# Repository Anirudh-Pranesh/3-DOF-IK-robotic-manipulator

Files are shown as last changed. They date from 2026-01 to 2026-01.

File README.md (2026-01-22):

# 3-DOF-Inverse-kinematic-robotic-manipulator

This project is an attempt at making a 3 degree of freedom robotic manipulator and implementing basic inverse kinematics

### Project contributors : 

- **Electronics and Programming :**
    -  Anirudh Pranesh - Eletronics and communication engineering department, National Institute of Technology Karnataka,  batch of 29'
- **Mathematical analsyses and assistance :** 
    - Neo Anil Dodti - Electronics and communication engineering department, National Institute of Technology Karnataka, batch of 29'
    - Aman Tandon - Electronics and communication engineering department, National Institute of Technology Karnataka, batch of 29'
- **Mechanical design :**
    - Maxon David Nazareth - Mechanical engineering department, National Institute of Technology Karnataka, batch of 29'

## The robotic manipulator and degrees of freedom 

The arm like structure of an industrial robot which is used to manipulate materials without direct physical ccontact by the operator is known as a robotic manipulator. A 3 degree of freedom robotic manipulator 
is designed to mimic the movement of a human arm. The motions achieved by the shoulder, elbows and wrists in a human arm is replicated in robotics using **joints**, **links**, **actuators**, and **end-effectors**

The image below depicts what an industrial grade robotic manipulator looks like



The degrees of freedom (DOF) of a manipulator is one of its defining features and is an important measure of the manipulators mobility and flexibility.

The degree of freedom is the number of independent moements the robot can make. 

## Introduction to the components of a manipulator and the initial design

The components that together constitute a robotic manipulator are **joints**, **links**, **actuators**, and **end-effectors**

1. Joint: A connection between two links that allows relative motion
    - Prismatic joint : Translation / sliding along one axis. Actuating the joint makes it longer/shorter
    - Revolute joint : A rotational joint (analogous to an elbow) that rotates about one degree of freedom
    - Spherial joint : A spherical joint can move in multiple degrees of freedom around a single point (analgous to the shoulder)
2. Link: A rigid body that connects joints and transmits motion and force
3. Actuator: A device that provides motion or force to drive a joint
4. End-effector: The terminal device attached to the last link that performs the task (for example a gripper / a scientific tool)

**The initial design :**

For a 3 DOF robotic manipulator, we fixated on 3 revolute joints. One to act as the shoulder and rotate about the y-axis. The 2nd to again act as a shoulder and rotate about the x-axis and the 3rd to act as the elbow, hence giving us access to any point in 3D space

We chose two, SG90 9g servos and one Futaba S3003 sero motor as the actuators. Ideally an actuator with a cycloidal gearbox should have been used. It offers very little backlash, and converts the high speeds of motors into higher torque to prevent the arm on collapsing on itself (An issue which was encountered later in the development process). However we went with the servo motors due to budget and time constraints.

For the links, we designed two I-beams in Fusion 360 that have a slot to attach the gear of the servo motor, and a hole on the other end to attach the end-effector / the servo motor for the elbow. 

In the end, after multiple centre of mass analsyes in Fusion 360, we determined the arm was stable and went with 3D printing it. We chose our material to be PETG with a 25% infill. 

9AA72045-951F-4C17-9807-37681B96CB96

759E43AC-6026-4F62-A465-EB66088A091E

https://github.com/user-attachments/assets/e654b260-f733-496b-b24b-751bba9cb4f4

## Forward vs Inverse kinematics

In forward kinematics, the operator manually sets the angles at which each joint should be rotated to, in order for its end-effector to reach a particular orientation/location in space.

However in inverse kinematics, the robot is aware of the final orientation/location its end-effector should be at, and it accordingly calculates at what angle each joint should be rotated to. 

For a 3-DOF manipulator, the math is relatively simple, involving inverse trigonometric functions and the cosine rule. However upon increasing the degrees of freedom the math becomes much more complex, involving linear algebra and transformations. 

## Real world applications 

A robotic manipulator is a quintessential technological system in the medical field. They are used in surgical robots and prosthetics. 

These are also often seen in industrial manufacturing processes and also used in space exploration missions. 

All these applications use inverse kinematics and hence it is clearly evident why understanding IK is cornerstone for working towards a career in robotics.

## Electronics and Programming - Inverse kinemtaics implementation 

The entire system is controlled using an arduino uno microcontroller. A unity simulation was set up to form the logical layer. Hence the rotation of each joint calculated via inverse kinematics in unity is obtained and sent to arduino using serial communication, and hence the angles are set to the servo motors using the Servo.h library. 

Here is the specific part of the code that performs the inverse kinematics calculations : 

```C#
// Obtaining traget position 
xf = Target.position.x;
yf = Target.position.y;
zf = Target.position.z;

r = Mathf.Sqrt(Mathf.Pow(xf, 2) + Mathf.Pow(zf, 2)); // Magnitude of the projection of the position vector of final point on the XZ plane
l = Mathf.Sqrt(Mathf.Pow(r, 2) + Mathf.Pow(yf, 2)); // Magnitude of the position vector of the final point

//l1 and l2 are the link lenghts

phi =  Mathf.Acos(((l*l)+(l1*l1)-(l2*l2))/(2*l1*l)) * Mathf.Rad2Deg; // Angle of the first link with respect the the position vector of the final point using cosine rule
theta = Mathf.Atan2(yf, r) * Mathf.Rad2Deg; // angle of the position vector of the final point with the XZ plane

Quaternion a = Quaternion.Euler(0, (180 + Mathf.Atan2(xf, zf) * Mathf.Rad2Deg), 0); // Setting angle for the base (shoulder) joint
Quaternion b = Quaternion.Euler(phi + theta, 0, 0); // Setting angle for the first link 
Quaternion c = Quaternion.Euler(-2 * phi, 0, 0); // Setting angle for the 2nd link (2 * phi assuming the two lengths are equal which it is in our case by design)

// Spherical linear interpolation for a smooth look
transform.localRotation = Quaternion.Slerp(transform.localRotation, a, t * Time.deltaTime);
base_joint.localRotation = Quaternion.Slerp(base_joint.localRotation, b, t * Time.deltaTime);
elbow_joint.localRotation = Quaternion.Slerp(elbow_joint.localRotation, c, t * Time.deltaTime);
```

Here is the fully working simulation : 

https://github.com/user-attachments/assets/3f60e0b6-7de5-4177-973a-fe10abcc836b

## Assembly

Once the 3D printed parts arrived, several **MAJOR** flaws in the mechanical design were immediately obvious.

First and foremost the parts were much heavier than anticipated. In hindsight it would have been a smarter move to make the links thinner and lesser in length
Secondly, the holes made for the gear of the servo motor to slot in were missing gear teeth, hence it was impossible to make the link rotate with the servo motor
Thirdly, the holes made for the servo motor to slot in at the joints had too less clearance

All in all the design was not optimal for the actuators we chose. 

A29553D9-5106-4DBB-A082-6044CEA94357

With some clever engineering, the plastic servo horns that came with the motors were attached to the links using strong rubber bands, and thankfully the link was able to rotate with the motor.

This however led to another issue. Due to the weight of the print being much higher than expected, our initial torque calculations went wrong. The SG90 servo could not provide enough torque at the shoulder to support the first link along with the 2nd link and the elbow joint. Hence, we used the S3003 servo motor with a much higher torque capacity to be the actuator at the shoulder. 

This proved to work and we had achieved 2 degrees of freedom for the robotic manipulator.

However we could not achieve the 3rd degree of freedom. The entire arm was attached to a circular disk which was mounted on to a singular servo motor for the rotation of the manipulator about the y axis. 

The motor could not sustain the weight of the entire system and the disk toppled. Many measures were taken in order to mitigate the ordeal. For example adding counter weights using metal. 
These efforts proved to be futile and we could not achieve the 3rd DOF. The gripper could not be attached either due to further excessive weight.  

We decided to work with the 2 DOF's we had and tweaked the code a little bit to achieve IK with it.

Here is the code for the unity simulation for 2 DOF manipulator : 

```C#

yf = Target.position.y;
zf = -Target.position.z;

r = Mathf.Sqrt(Mathf.Pow(yf, 2) + Mathf.Pow(zf, 2));

phi = Mathf.Atan2(yf , zf) * Mathf.Rad2Deg;
theta = Mathf.Acos(((r * r) + (l1 * l1) - (l2 * l2)) / (2 * l1 * r)) * Mathf.Rad2Deg;

base_joint.localRotation = Quaternion.Euler(phi + theta, 0, 0);
elbow_joint.localRotation = Quaternion.Euler(-2*theta, 0, 0);

intAngle1 = (int)(phi+theta)-11;
intAngle2 = (int)(2*theta);
strAngle1 = intAngle1.ToString();
strAngle2 = intAngle2.ToString();
relay = strAngle1 + " " + strAngle2;
serial.WriteLine(relay);

```

Here is the image of the disk barely balancing on the servo motor. It may be used as a proof of concept for a 3 DOF manipulator with our design : 



# Final project showcase : 

https://github.com/user-attachments/assets/3d56ba8f-9d47-44a3-8794-81a7bd2c54c0

# Learning outcomes 

- The mechanical design itself has no flaw. However more rigorous testing must be done before going ahead with the 3D print. For instance performing mechanical simulations like finite element analsysis.
- A basic, but in depth understanding of robotic manipulators and the math lying behind it
- A basic introduction to DH parameters
- Exposure to alternative robotic simulation software like coppeliaSim (was not used due to logistical and time constraints)
- Achieved an understanding of practical applications of robotic manipulators in everyday life and how they can be integrated with other robotic systems

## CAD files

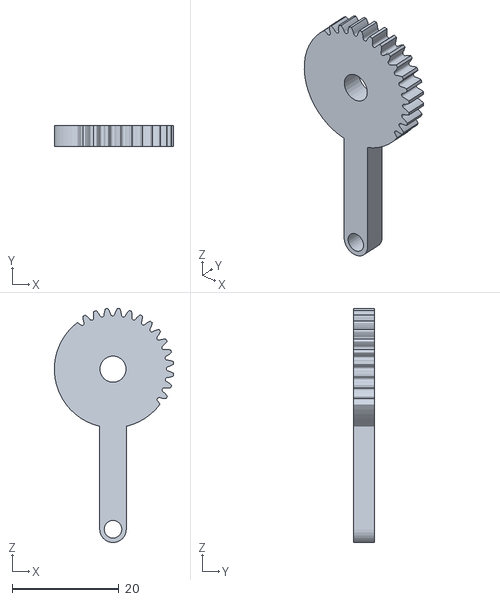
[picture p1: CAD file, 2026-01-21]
STL files/3dprint/gripper4.stl
22.4 x 4.00 x 43.8

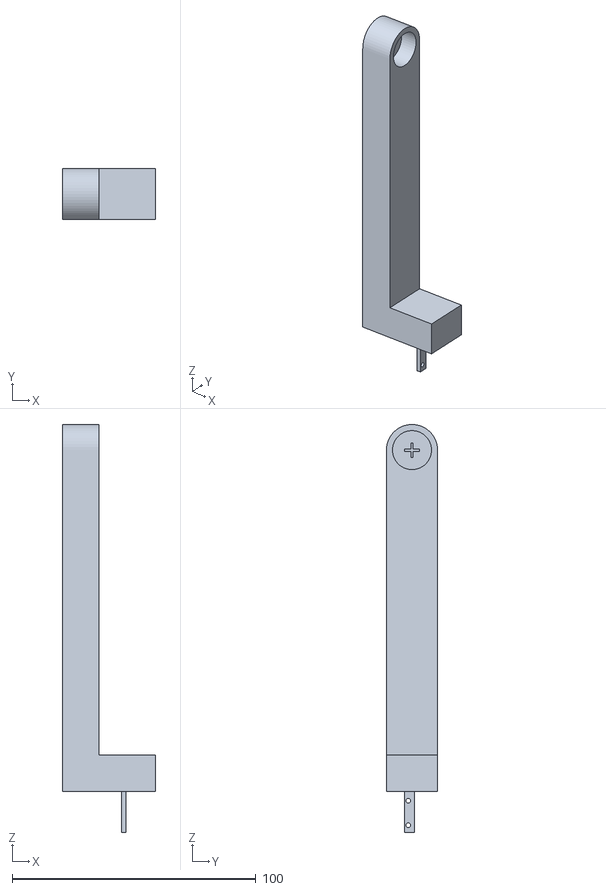
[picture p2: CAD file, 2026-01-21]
Unity/Assets/arm2.obj
38.0 x 21.0 x 167.2

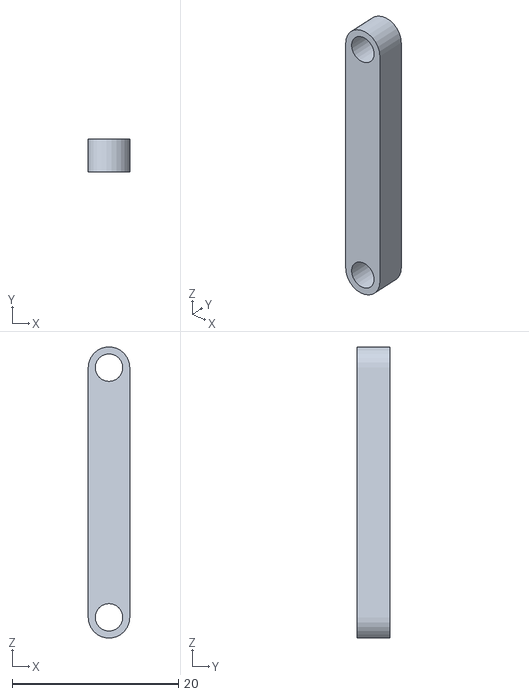
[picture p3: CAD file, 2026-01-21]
STL files/3dprint/gripper3.stl
5.00 x 4.00 x 35.0

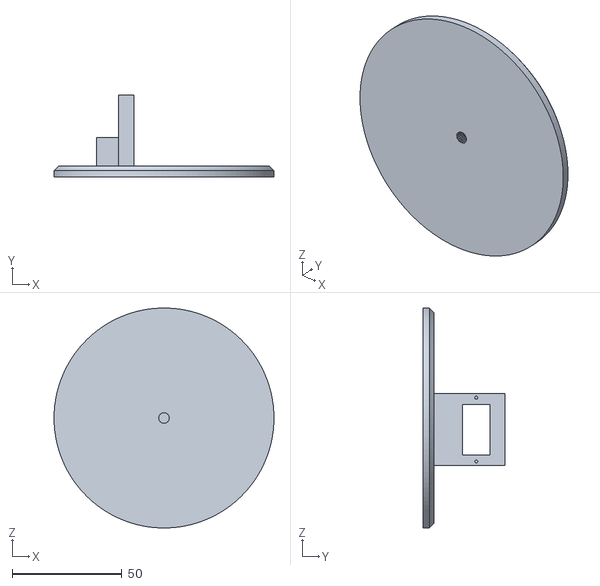
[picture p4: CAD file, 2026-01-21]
Unity/Assets/base1.obj
100.0 x 37.4 x 100.0

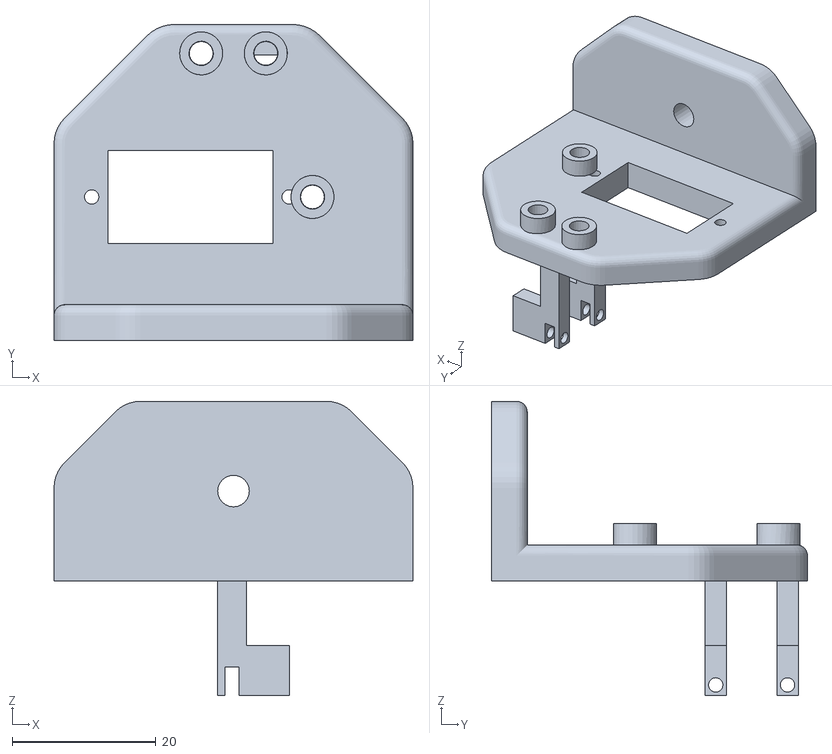
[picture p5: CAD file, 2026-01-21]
STL files/3dprint/gripperbody.stl
50.0 x 44.0 x 41.0

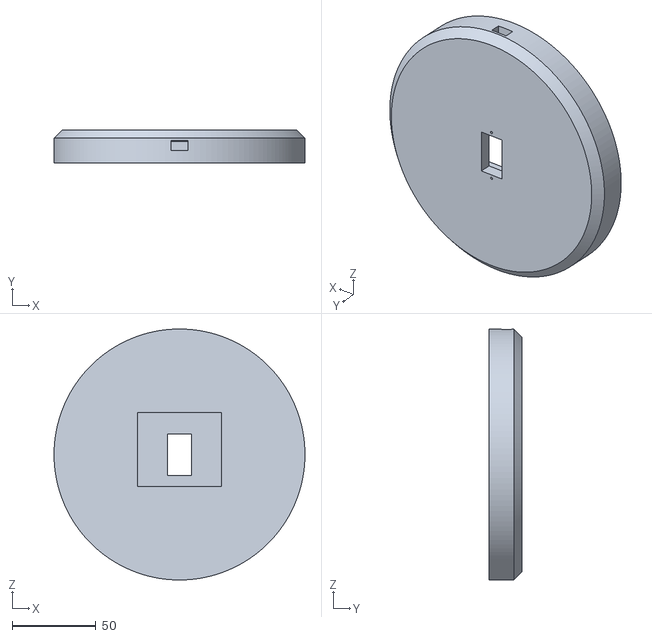
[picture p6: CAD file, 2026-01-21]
Unity/Assets/base2.obj
150.0 x 20.0 x 150.0

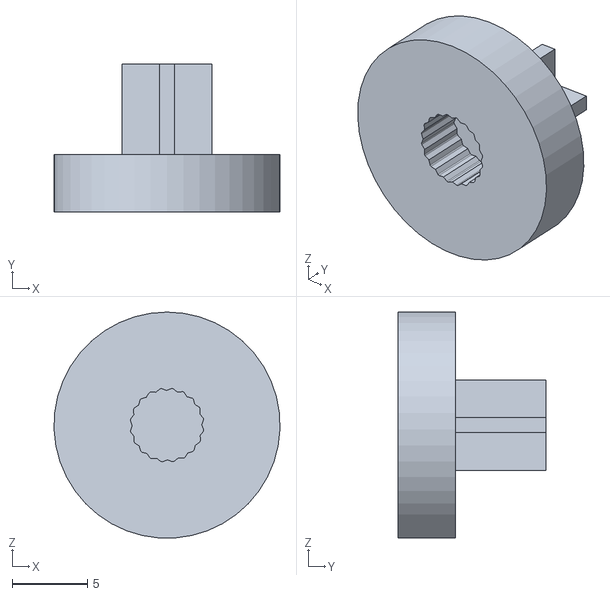
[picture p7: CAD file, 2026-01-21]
STL files/3dprint/plus1.stl
15.0 x 9.80 x 15.0

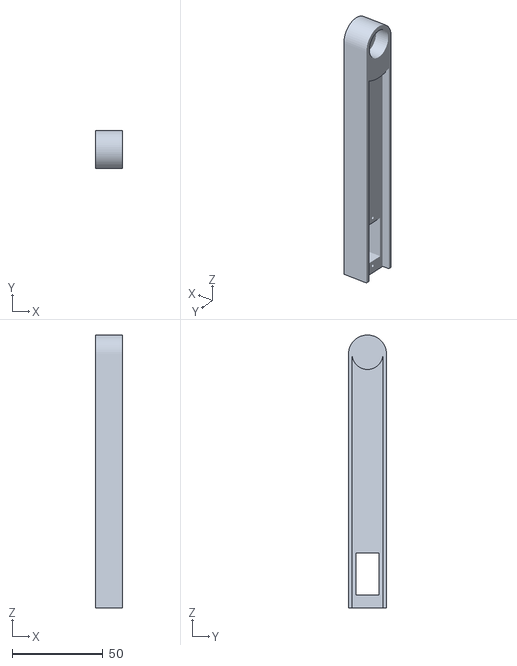
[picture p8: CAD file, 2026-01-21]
Unity/Assets/arm1.obj
15.0 x 21.0 x 150.5

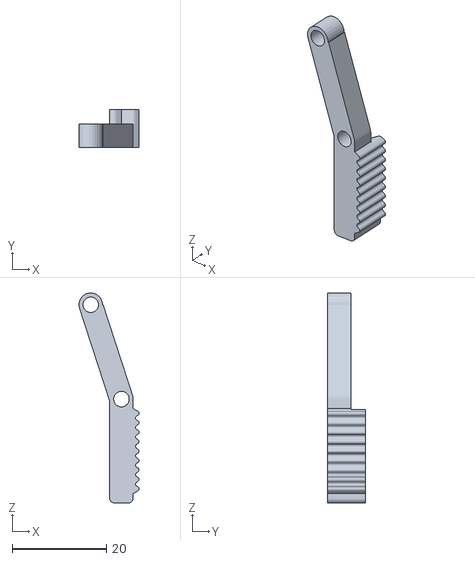
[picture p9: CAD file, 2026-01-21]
STL files/3dprint/gripper5.stl
12.7 x 8.00 x 44.5

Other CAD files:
STL files/3dprint/gripper6.stl
STL files/3dprint/gripper2.stl
STL files/3dprint/gripper1.stl
STL files/3dprint/base1.stl
STL files/3dprint/arm2.stl
STL files/3dprint/base2.stl
STL files/3dprint/plus2.stl
STL files/3dprint/arm1.stl

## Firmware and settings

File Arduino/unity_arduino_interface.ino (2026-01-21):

#include <Servo.h>

Servo base;
Servo elbow;
String input = "";
int angle1 = 0;
int angle2 = 0;

void setup() {
  // put your setup code here, to run once:
  Serial.begin(9600);
  Serial.setTimeout(100);
  base.attach(6);
  elbow.attach(5);
  //base.write(0);
  //elbow.write(0);
}

void loop() {
  input = Serial.readStringUntil('\n');   // read full line
  int spaceIndex = input.indexOf(' ');    // find space
  String first = input.substring(0, spaceIndex);
  String second = input.substring(spaceIndex + 1);

  angle1 = first.toInt();
  angle2 = second.toInt();

  base.write(30+angle1);
  elbow.write(180-angle2);


}

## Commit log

2026-01-21 All file upload
    [arm1.stl, arm2.stl, base1.stl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]
2026-01-21 unity upload
    [arm1.obj, arm2.obj, base1.obj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]
